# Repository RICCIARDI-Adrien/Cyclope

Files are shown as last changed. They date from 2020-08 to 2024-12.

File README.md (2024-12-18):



# Cyclope

A little robot powered by a Raspberry Pi 3 A+, featuring a 8MPixel Raspberry Pi Camera V2 and a 360° lidar.  
A fast WiFi connection allows to remote control the robot while displaying camera real-time full HD video stream.  
A tailored Buildroot Linux distribution runs the software, controlled through WiFi through an embedded web server.

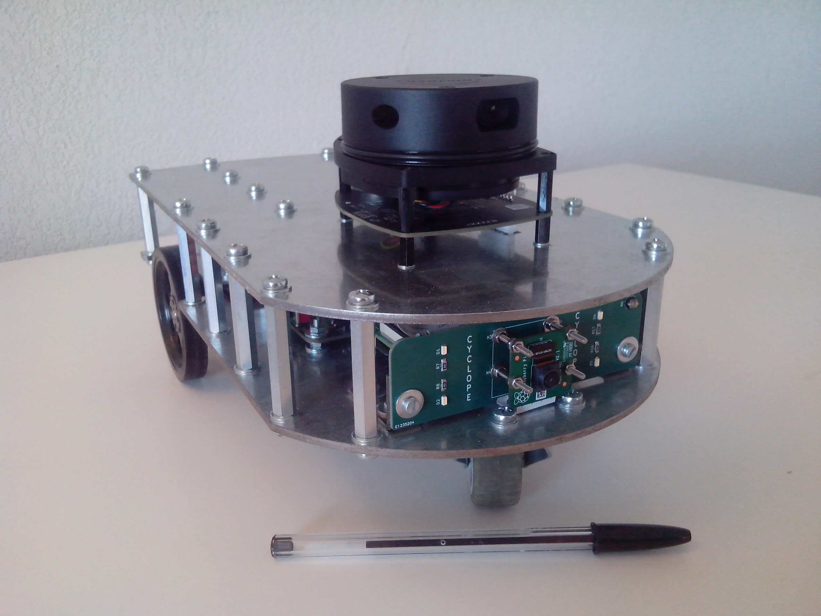
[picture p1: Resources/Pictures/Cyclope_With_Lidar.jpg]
Cyclope


## Hardware

PCB has been designed using KiCad 5.1.5 and has been ported to KiCad 6. All manufacturing files are available from [Release](https://github.com/RICCIARDI-Adrien/Cyclope/releases) page.  
A PDF version of the schematic is also provided.

## Software

Robot's Raspberry Pi is powered by a tailored [Buildroot](https://buildroot.org) Linux distribution.

### Getting sources

Clone the repository and the submodules all in the row :
```
git clone --recurse-submodules https://github.com/RICCIARDI-Adrien/Cyclope
```

### Building

Enter repository directory, clean previous build (if needed) and generate image :
```
cd Cyclope/Software/buildroot
make distclean
make BR2_EXTERNAL=$(realpath ..)/cyclope cyclope_defconfig
make
```

Generated image to burn to a SD card is `Cyclope/Software/buildroot/output/images/sdcard.img`.

## Mechanical

Chassis is made of two overlaid 3mm-thick steel plates.  
See [Mechanical_Dimensions.odg](Chassis/Mechanical_Dimensions.odg) file for additional design information.  
Provide the `Chassis.dxf` file from [Release](https://github.com/RICCIARDI-Adrien/Cyclope/releases) page to a metal laser cutting service.

## Supply parts

See `Bill_Of_Material.csv` file from [Release](https://github.com/RICCIARDI-Adrien/Cyclope/releases) page for PCB parts. All other needed mechanical and electrical parts are listed below.

### Electrical

* 2x servomotor : [Feetech FS5113R](https://www.gotronic.fr/art-servomoteur-fs5113r-25841.htm)
* 40-pin flat cable : [Amphenol FC40150-0](https://fr.farnell.com/amphenol/fc40150-0/cordon-2-54mm-f-f-150mm-40voies/dp/2217617)
* Battery holder : [EM8](https://www.gotronic.fr/art-coupleur-8-piles-lr6-em8-5718.htm), isolate apparent contacts but battery holder ones with adhesive tape to prevent them from touching chassis spacers

### Mechanical

* Front castor wheel : [Guitel 55031100](https://fr.rs-online.com/web/p/roulettes-industrielles/3064300).
* 2x servomotor support : [ASB01](https://www.gotronic.fr/art-support-de-servos-asb01-11637.htm).
* 2x servomotor wheel : [FS5103R-W](https://www.gotronic.fr/art-roue-pour-servomoteur-fs5103r-25857.htm).
* 2x front board flat angle bracket : NFLE2012-20.
* 21x chassis plates M4x40 hex female spacer : [Ettinger 05.04.401](https://fr.farnell.com/ettinger/05-04-401/entretoise-m4x40-vzk/dp/1466794).
* 4x M2x20 screw to attach camera to front board (use three nuts per screw). Using such long screws allow to further protect the camera.
* 12x M2 nut.
* 4x M2.5x25 screws to attach Raspberry Pi to chassis bottom plate (use three nets per screw).
* 12x M2.5 nut.
* 18x M3x10 screw :
  * 8x to attach both servomotors to their support.
  * 4x to attach the two supports to chassis bottom plate.
  * 4x to attach front board flat angle brackets to chassis bottom plate.
  * 2x to attach front board to flat angle brackets.
* 4x M3x15 screw to attach motherboard to chassis bottom plate (use three nuts per screw).
* 30x M3 nut.
* 47x M4x10 screw :
  * 21x to attach female spacers to chassis bottom plate.
  * 4x to attach castor wheel to chassis bottom plate.
  * 1x to prevent battery pack from escaping from robot bottom.
  * 21x to attach chassis top plate to chassis.
* 5x M4 nut.
* Use flat washers of appropriate dimensions if desired.

## Photo gallery

### Castor wheel

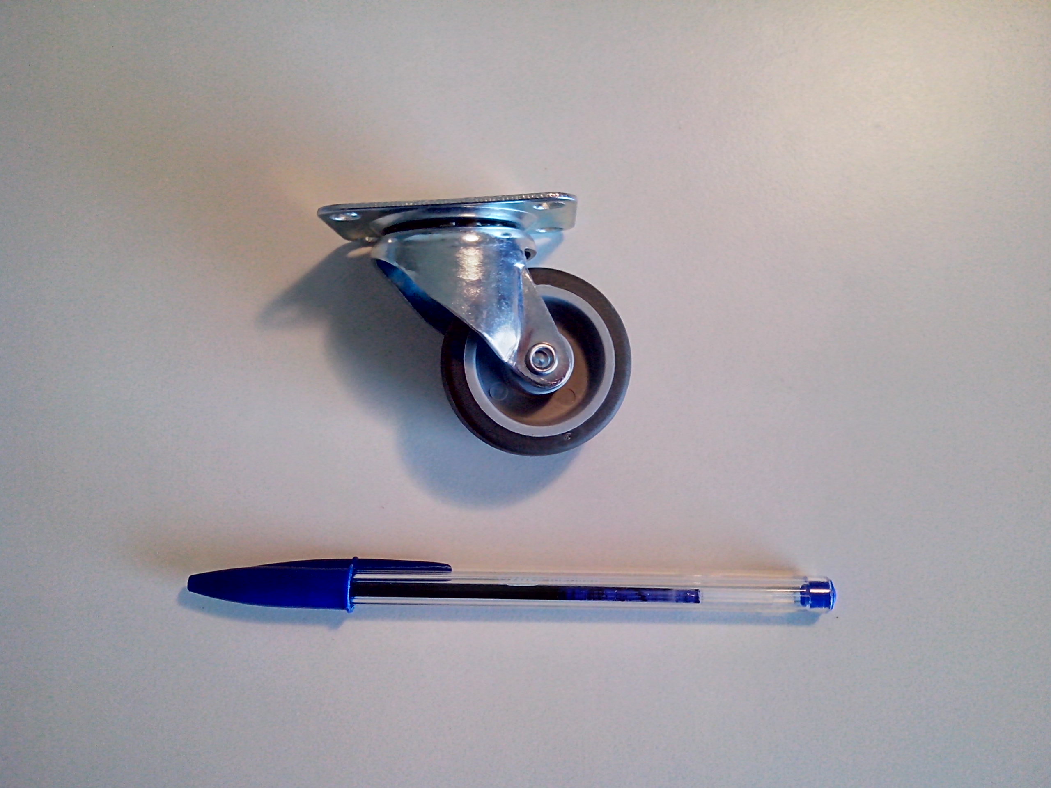
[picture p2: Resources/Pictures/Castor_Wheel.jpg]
Castor wheel


### Servomotor, wheel and support

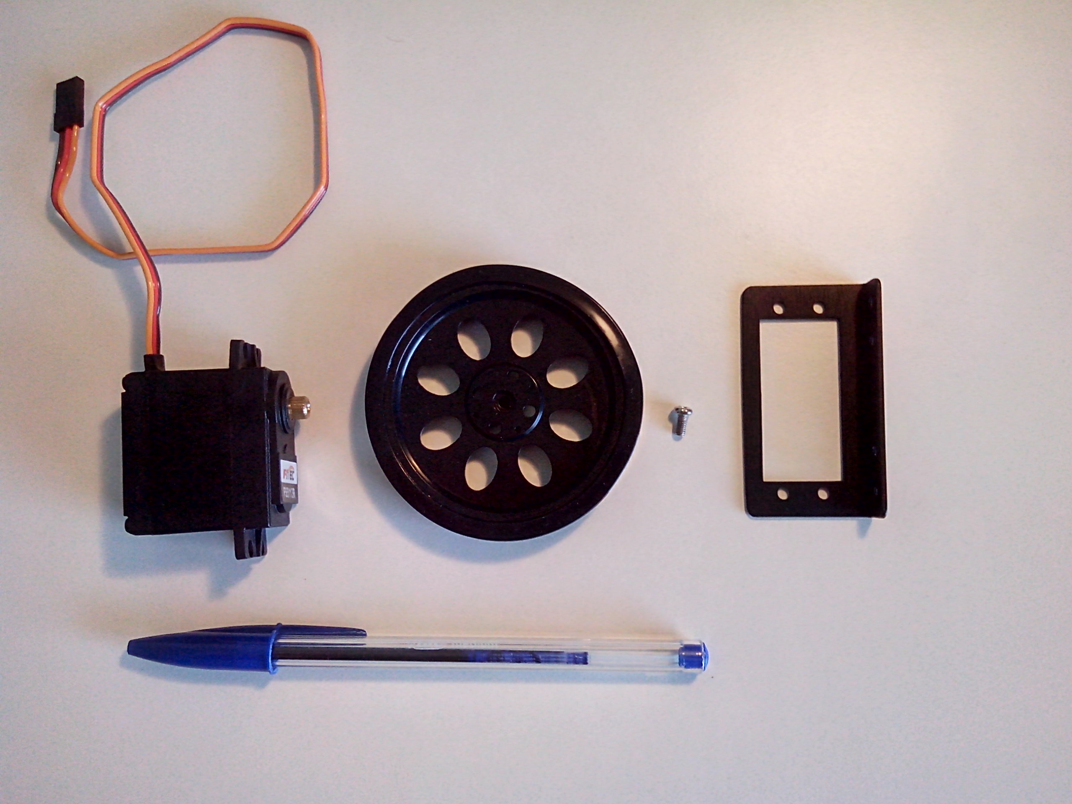
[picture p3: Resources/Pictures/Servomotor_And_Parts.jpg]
Servomotor, wheel and support


### Chassis

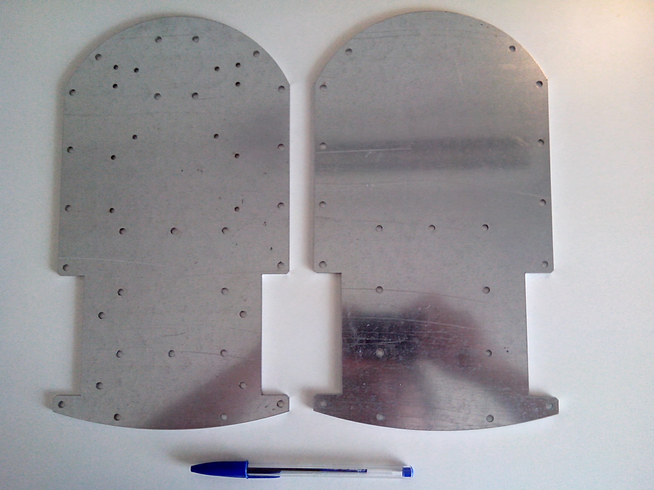
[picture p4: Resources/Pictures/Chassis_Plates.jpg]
Chassis plates

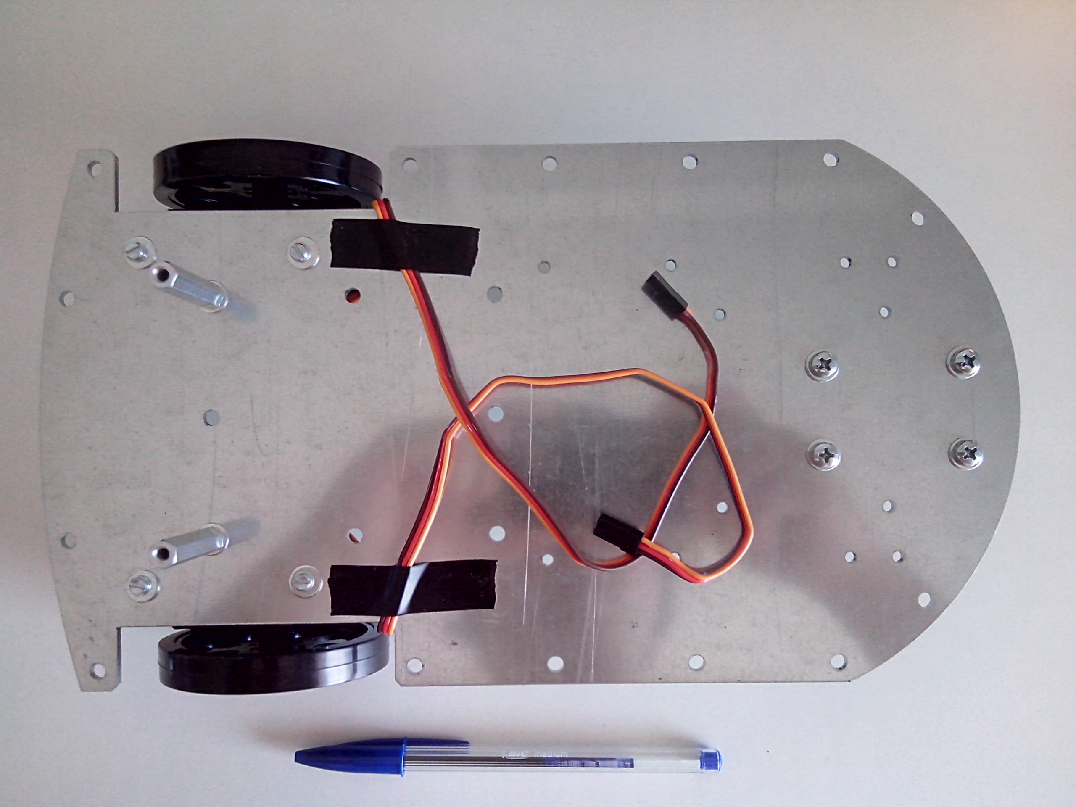
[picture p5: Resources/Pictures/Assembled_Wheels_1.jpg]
Assembled wheels 1

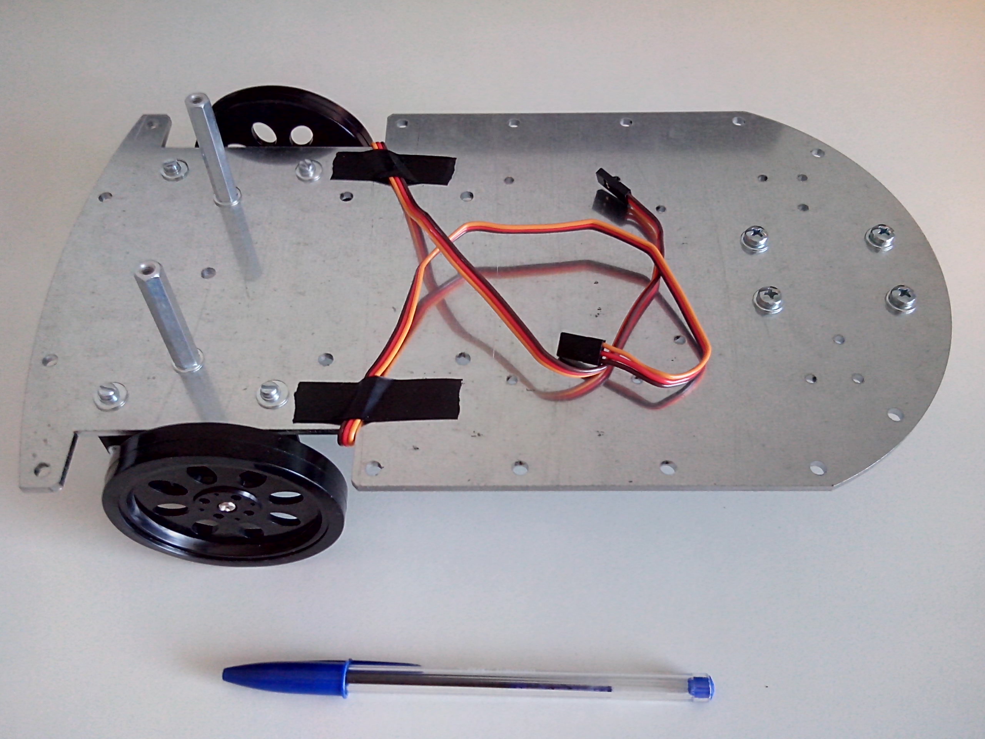
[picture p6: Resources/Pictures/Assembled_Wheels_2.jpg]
Assembled wheels 2

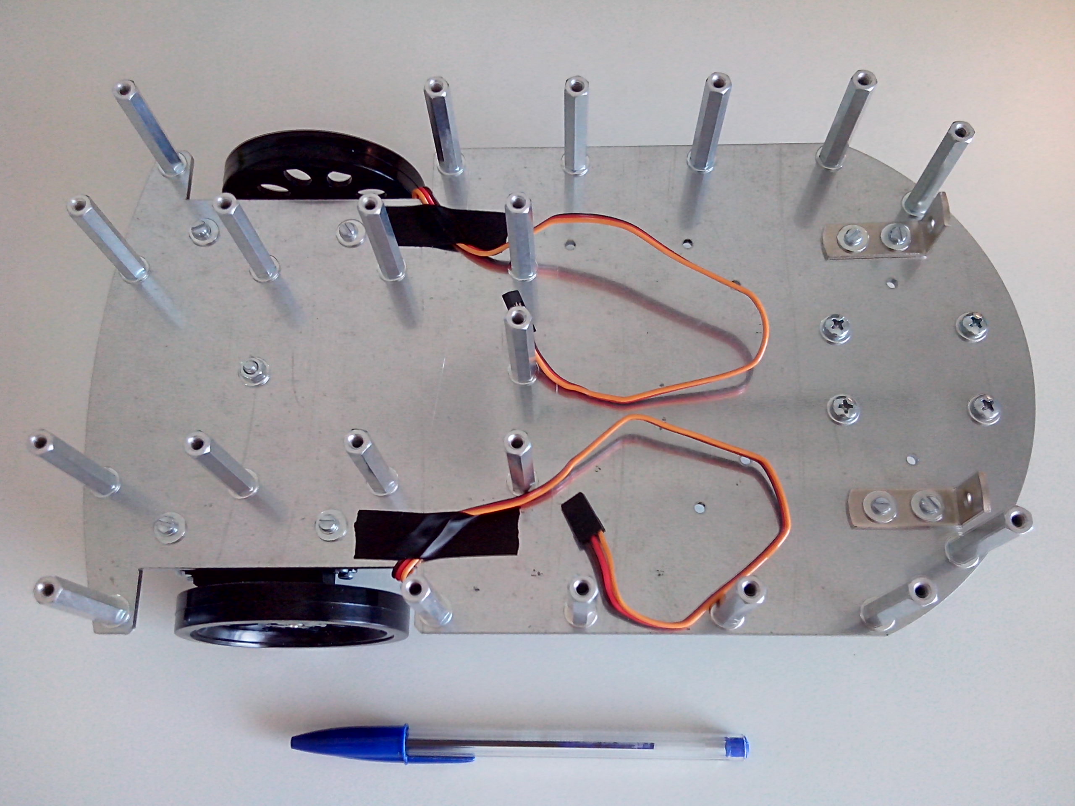
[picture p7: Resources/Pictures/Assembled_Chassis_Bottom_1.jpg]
Assembled chassis bottom 1

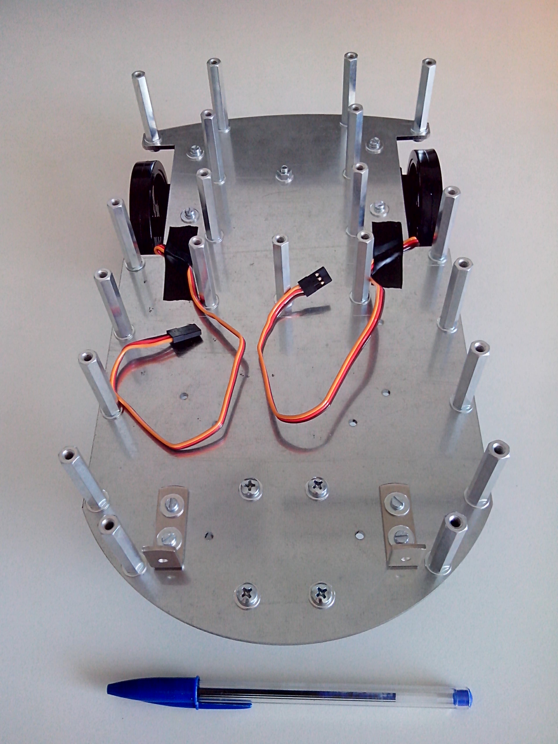
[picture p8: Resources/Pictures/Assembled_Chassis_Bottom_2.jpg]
Assembled chassis bottom 2


### PCB

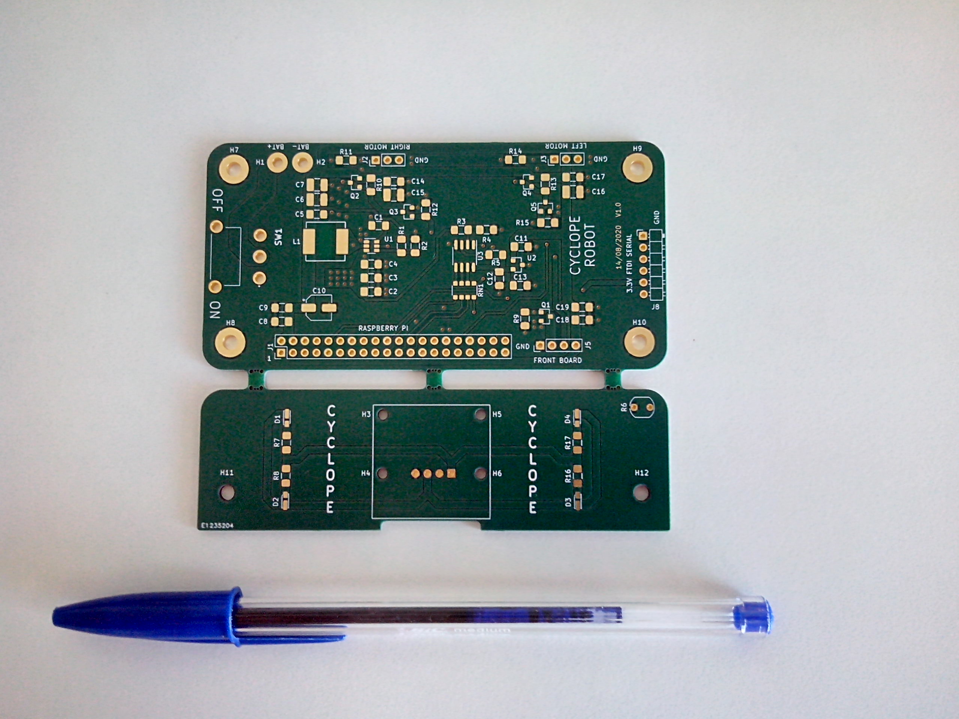
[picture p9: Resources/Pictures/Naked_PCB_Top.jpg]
Naked PCB top

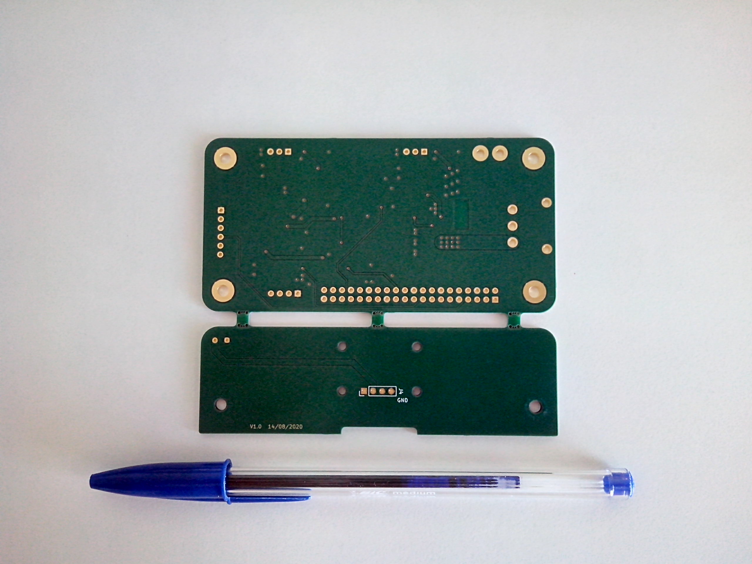
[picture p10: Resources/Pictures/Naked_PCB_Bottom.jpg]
Naked PCB bottom


### Motherboard

PCB has been soldered by hands (resistors array part was missing, I used normal 0805 resistors) :
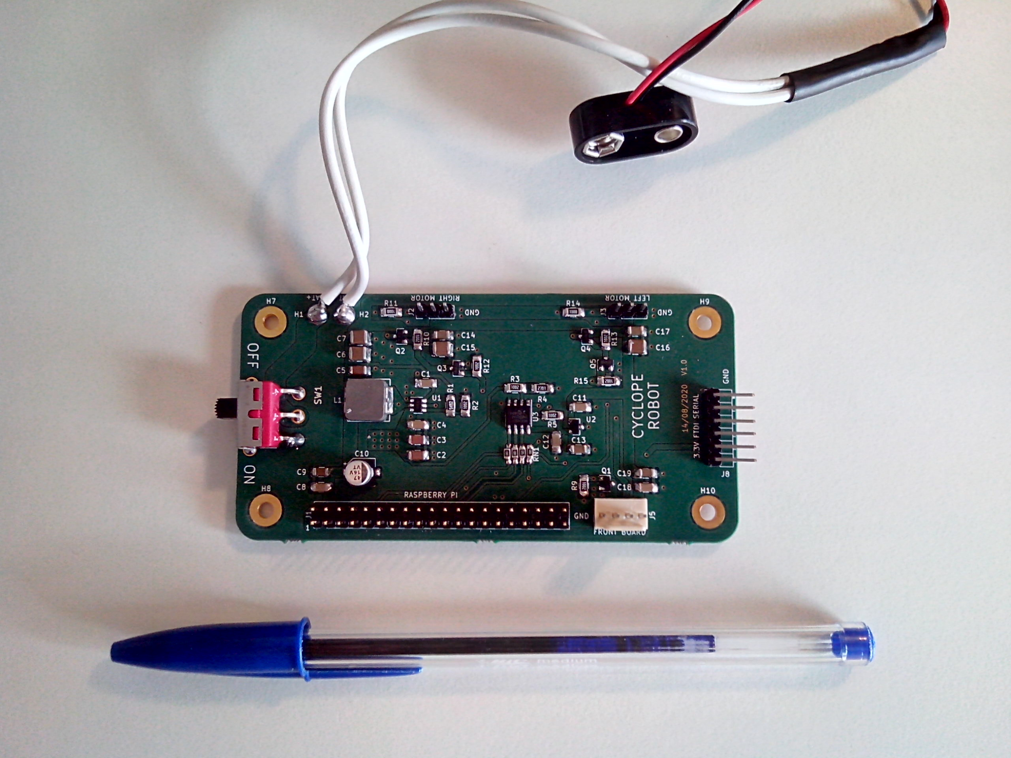
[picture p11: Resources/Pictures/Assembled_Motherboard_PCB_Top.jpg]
Assembled motherboard PCB top

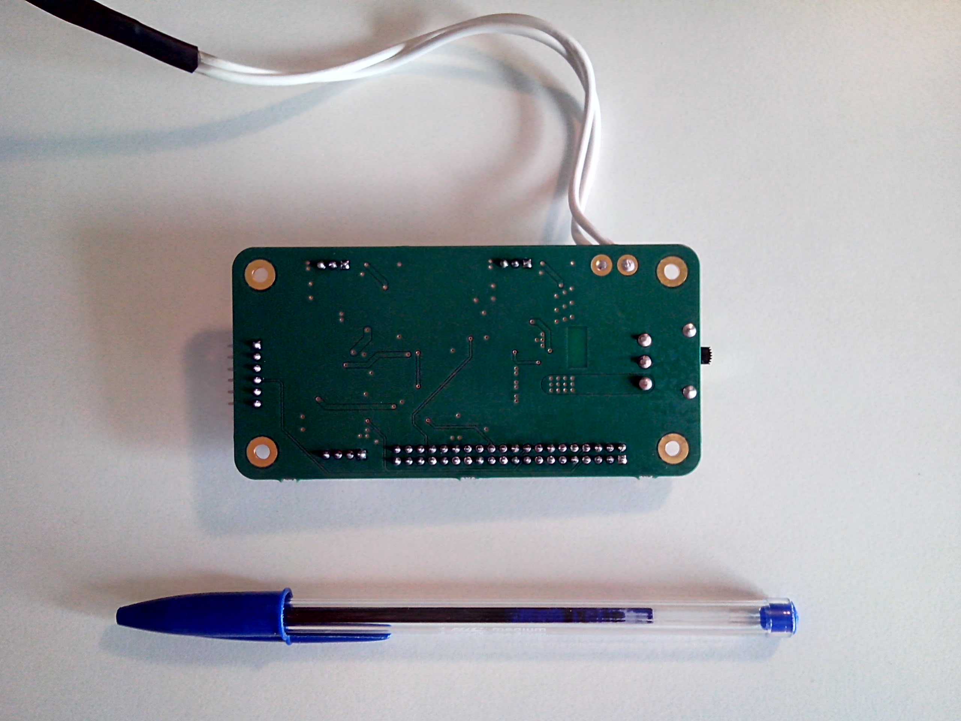
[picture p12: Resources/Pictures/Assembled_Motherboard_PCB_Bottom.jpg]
Assembled motherboard PCB bottom


A big capacitor has been added to keep battery voltage stable when a lot of current is required :
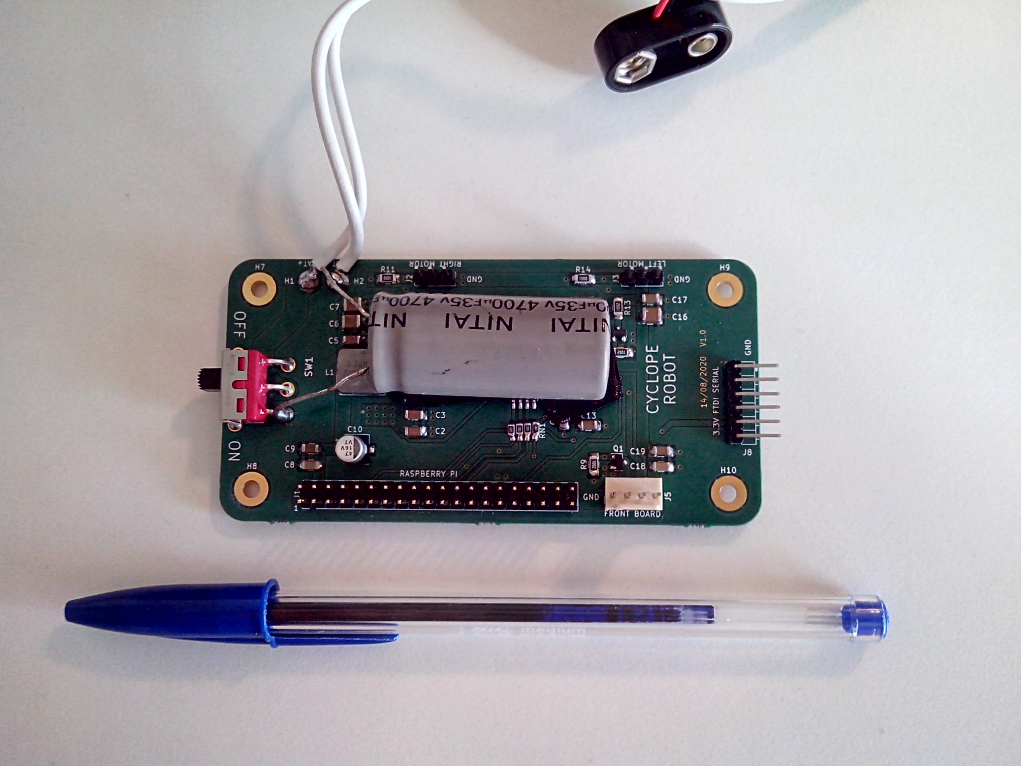
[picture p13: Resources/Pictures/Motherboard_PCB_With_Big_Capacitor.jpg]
Motherboard PCB with big capacitor


### Front board

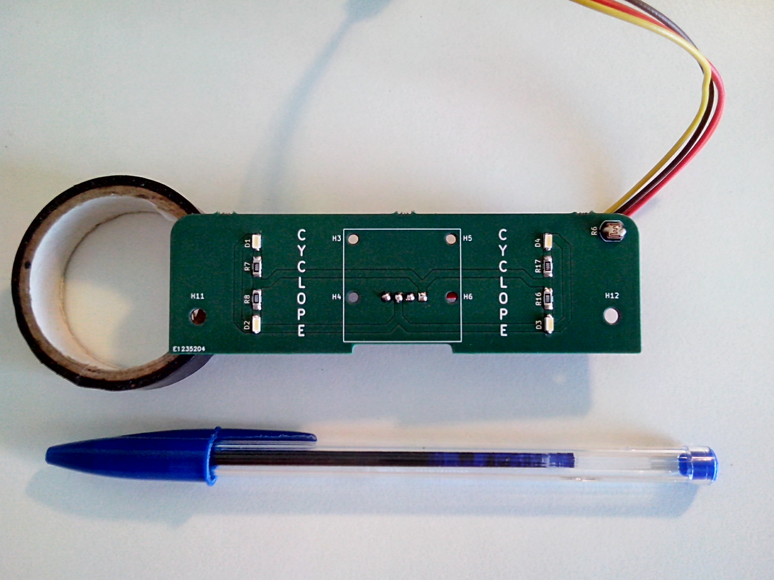
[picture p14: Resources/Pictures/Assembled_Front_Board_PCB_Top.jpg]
Assembled front board PCB top

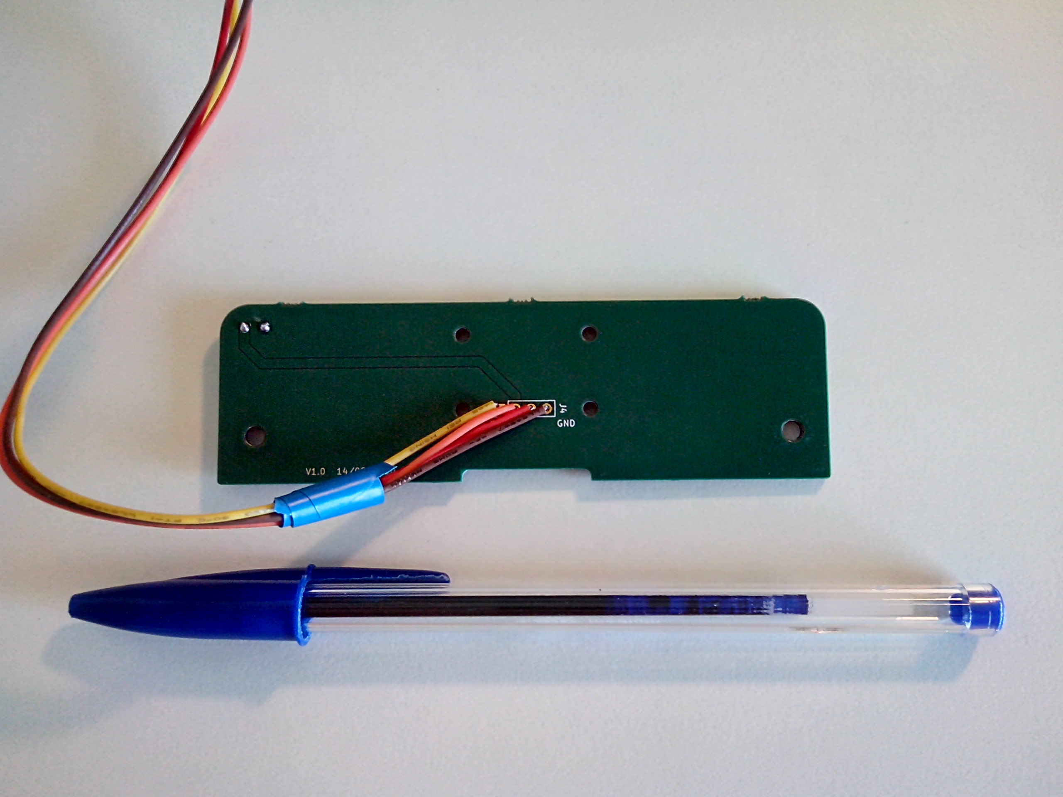
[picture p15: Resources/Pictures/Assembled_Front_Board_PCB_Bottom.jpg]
Assembled front board PCB bottom


With Raspberry Pi Camera V2 mounted :
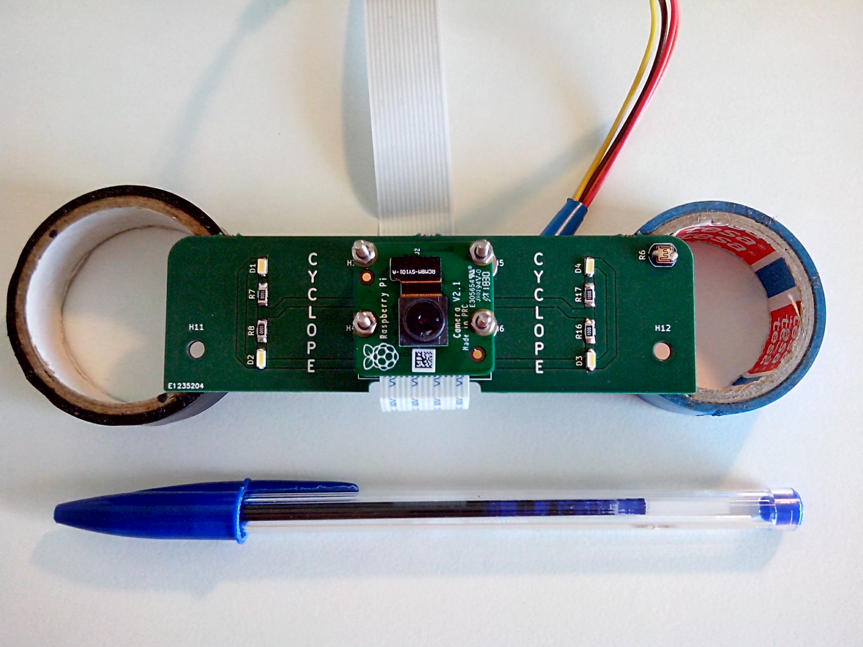
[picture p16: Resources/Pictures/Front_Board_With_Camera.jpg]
Front board with camera


### Assembled electronic boards

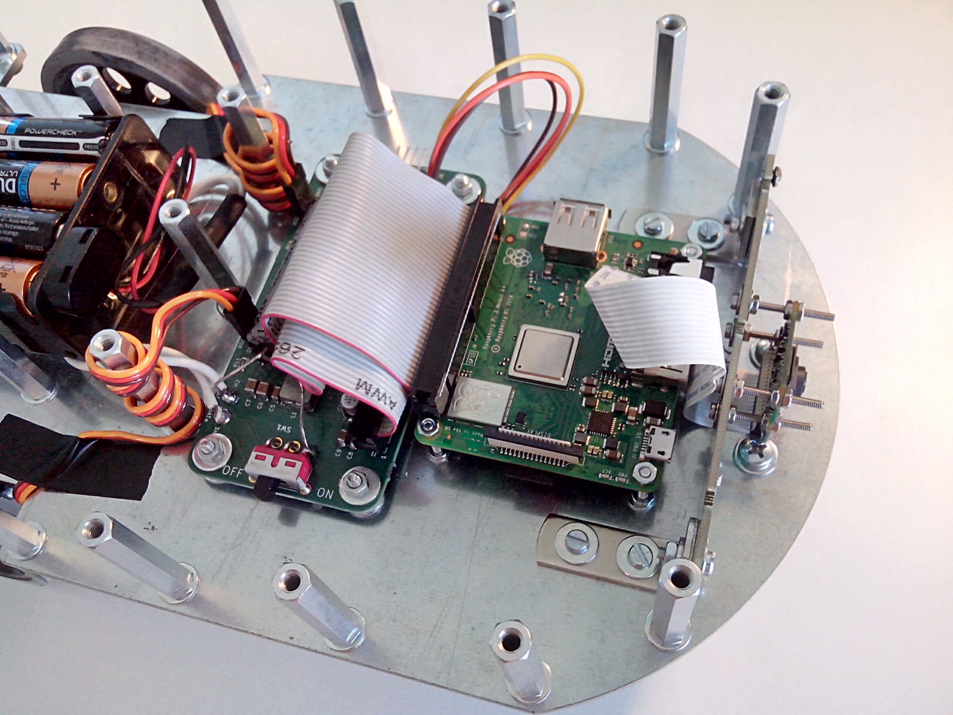
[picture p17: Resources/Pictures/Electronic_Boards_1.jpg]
Electronic boards 1

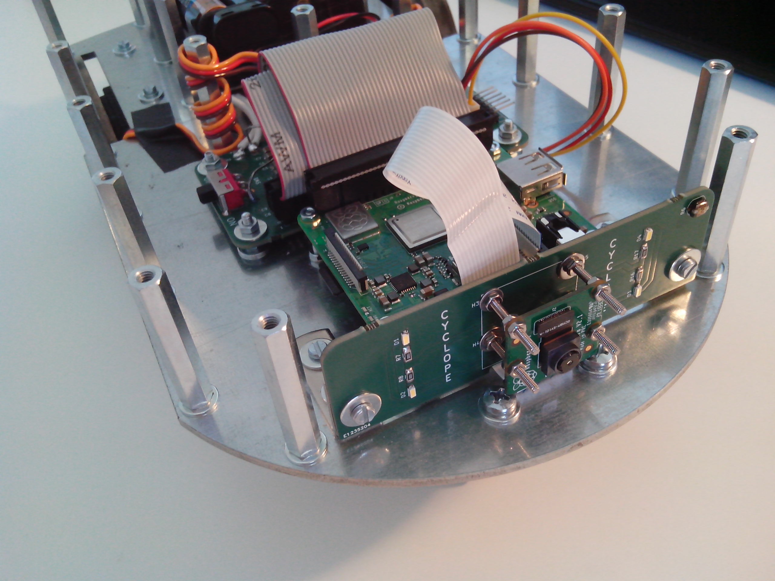
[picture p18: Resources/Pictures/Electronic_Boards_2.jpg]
Electronic boards 2

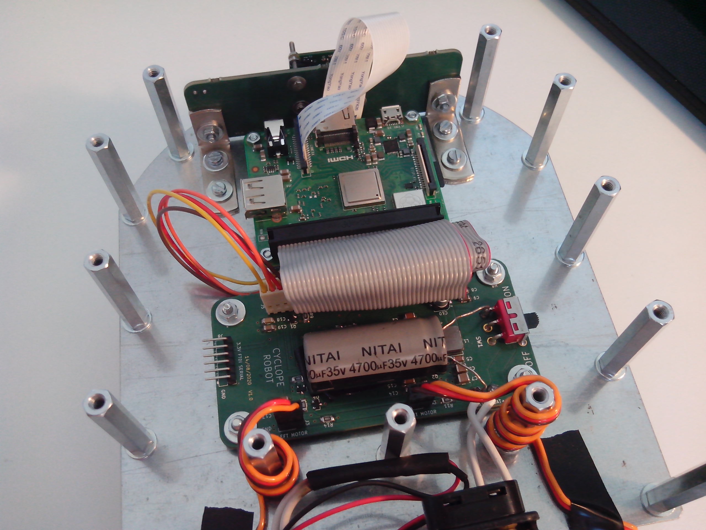
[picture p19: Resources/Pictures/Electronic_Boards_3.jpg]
Electronic boards 3

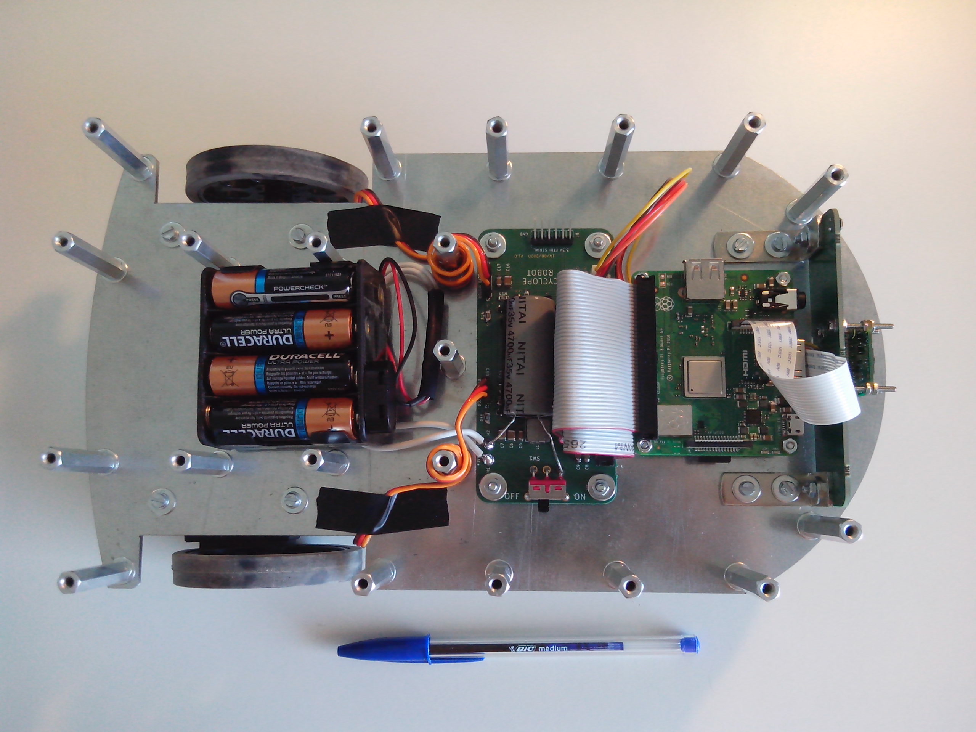
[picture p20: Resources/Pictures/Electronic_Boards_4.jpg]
Electronic boards 4

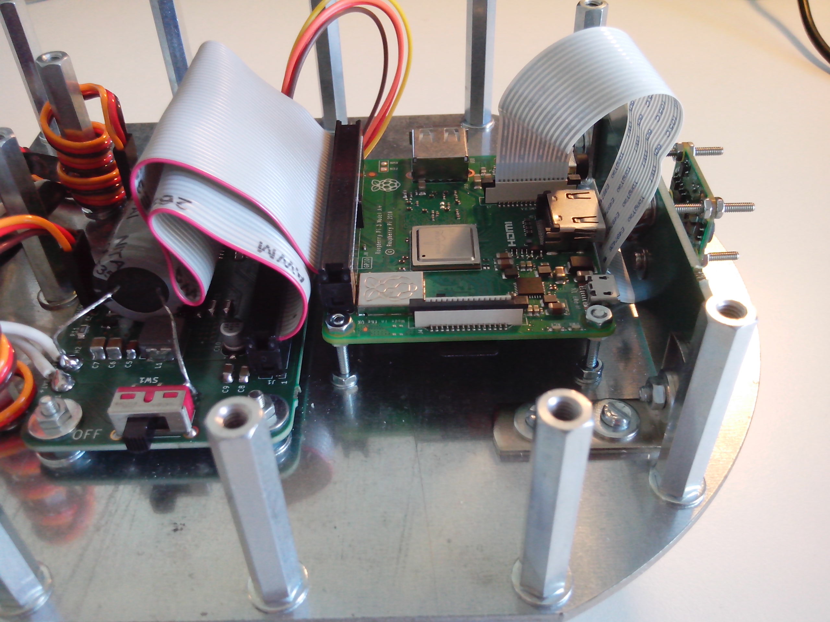
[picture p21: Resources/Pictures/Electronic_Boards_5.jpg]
Electronic boards 5


### Assembled robot

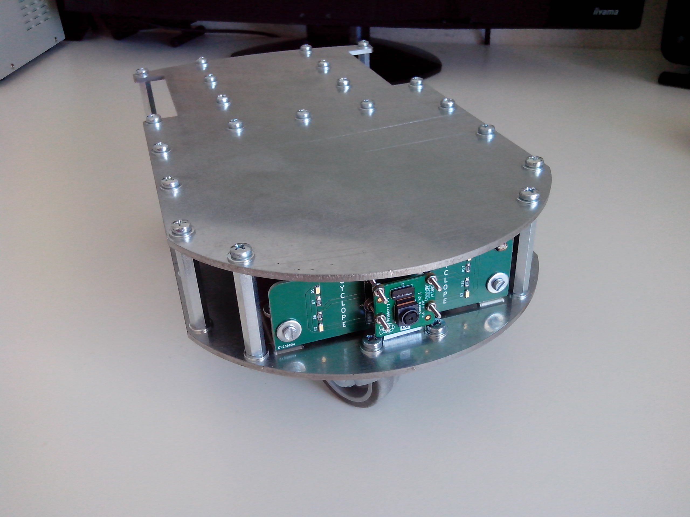
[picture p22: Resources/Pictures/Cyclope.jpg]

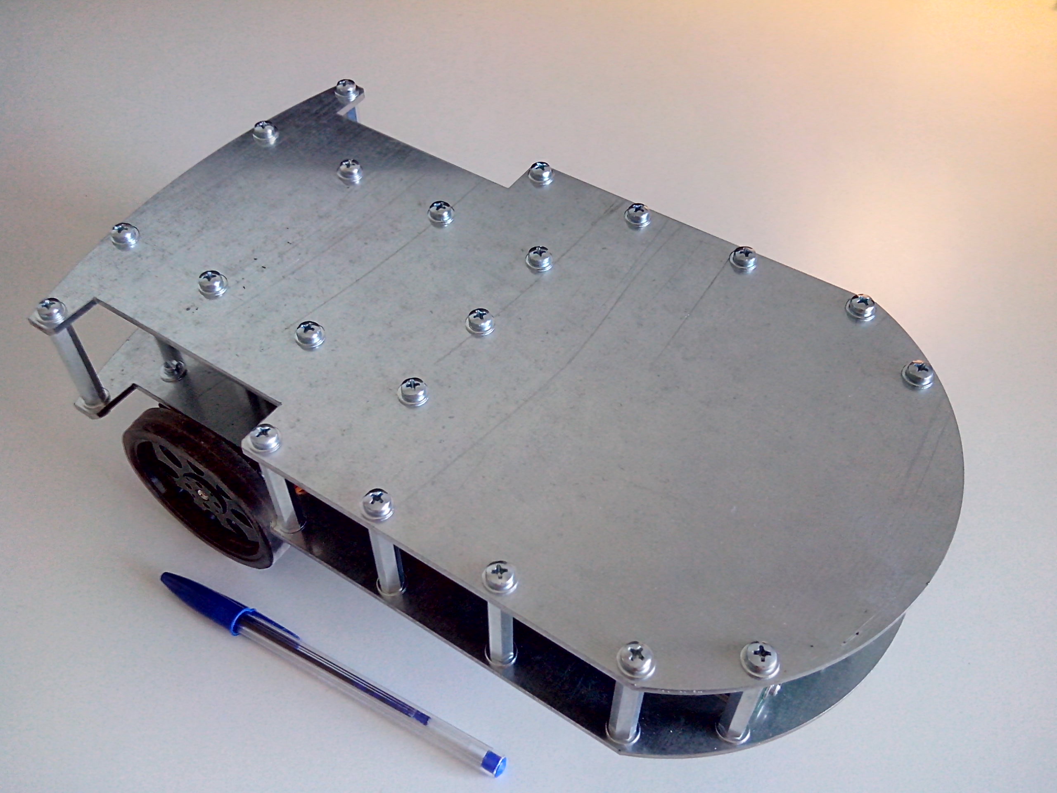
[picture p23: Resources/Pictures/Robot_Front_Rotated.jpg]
Robot front rotated

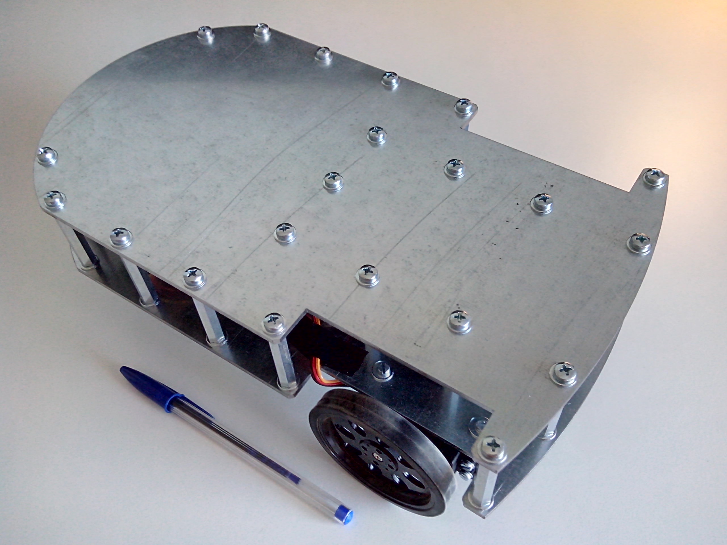
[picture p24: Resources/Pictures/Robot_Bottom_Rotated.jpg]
Robot bottom rotated

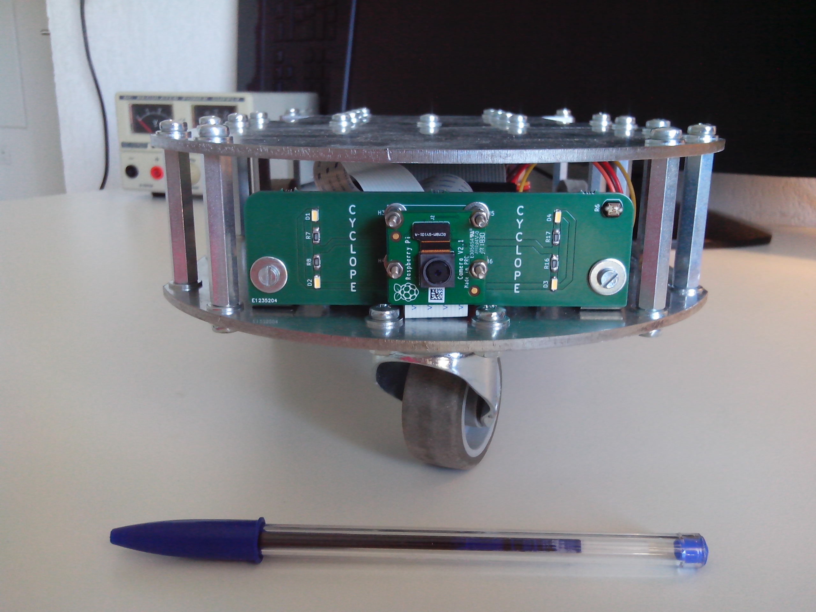
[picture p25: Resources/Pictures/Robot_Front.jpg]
Robot front

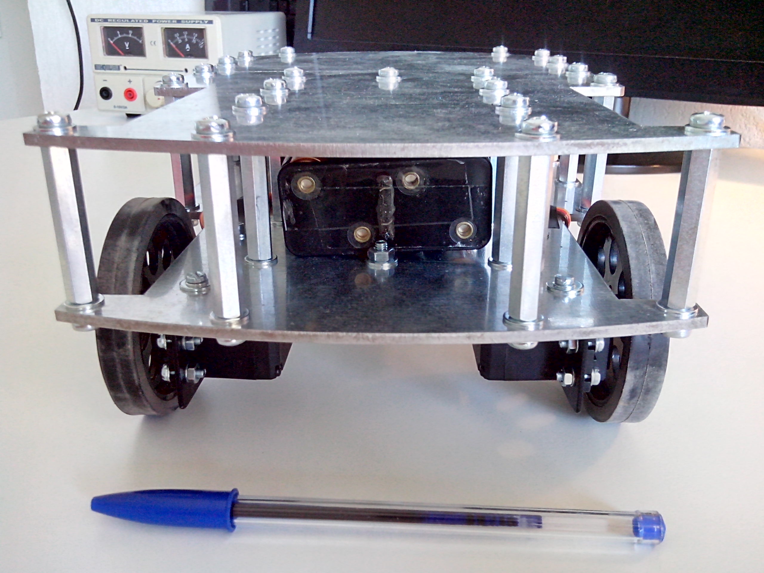
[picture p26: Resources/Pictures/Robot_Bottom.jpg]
Robot bottom

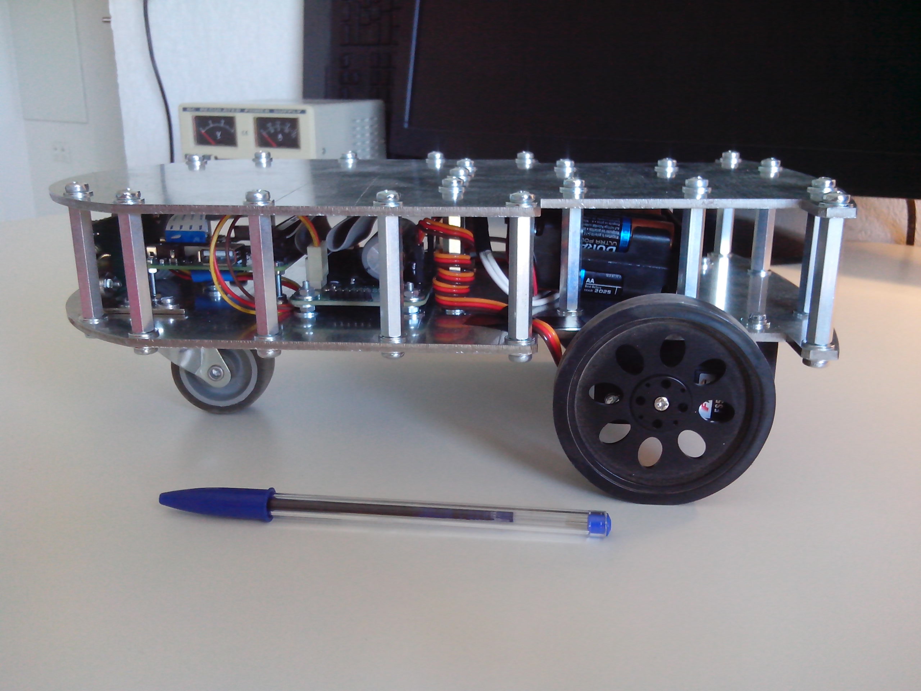
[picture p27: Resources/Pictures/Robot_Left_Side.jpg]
Robot left side

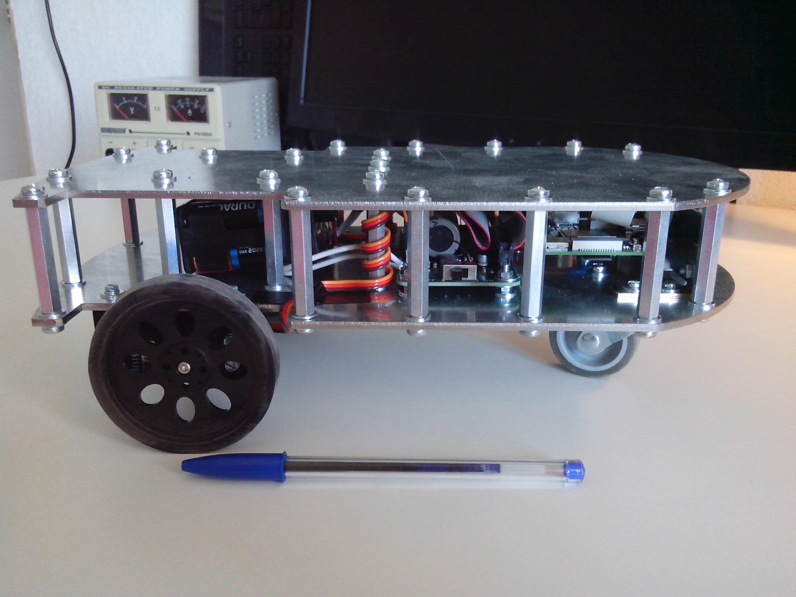
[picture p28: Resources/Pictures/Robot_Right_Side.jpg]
Robot right side


### Update for version 1.1 adding a 360° lidar

Chassis top plate with lidar holes :
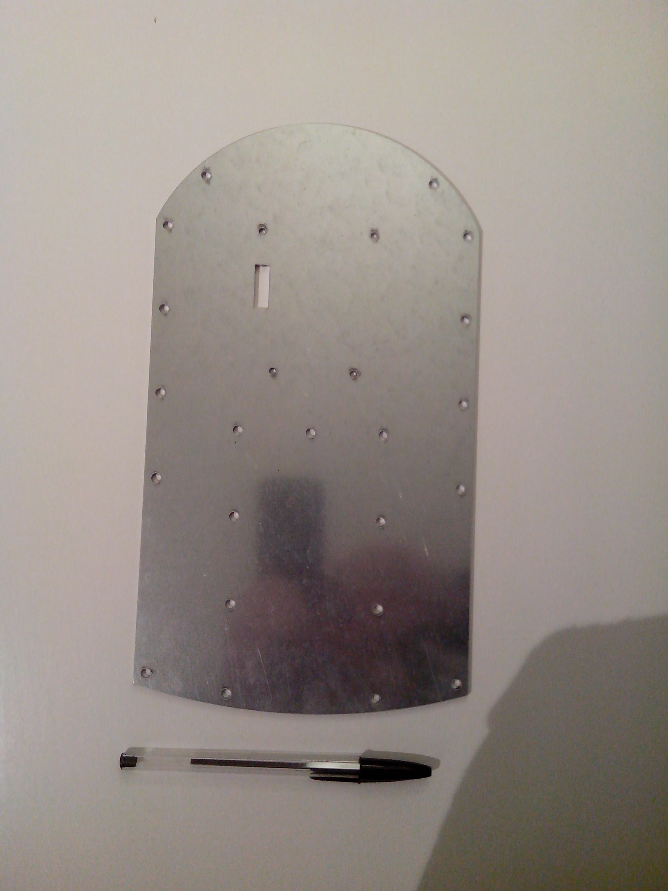
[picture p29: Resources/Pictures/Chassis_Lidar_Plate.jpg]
Chassis top plate


Lidar assembled on chassis top plate :
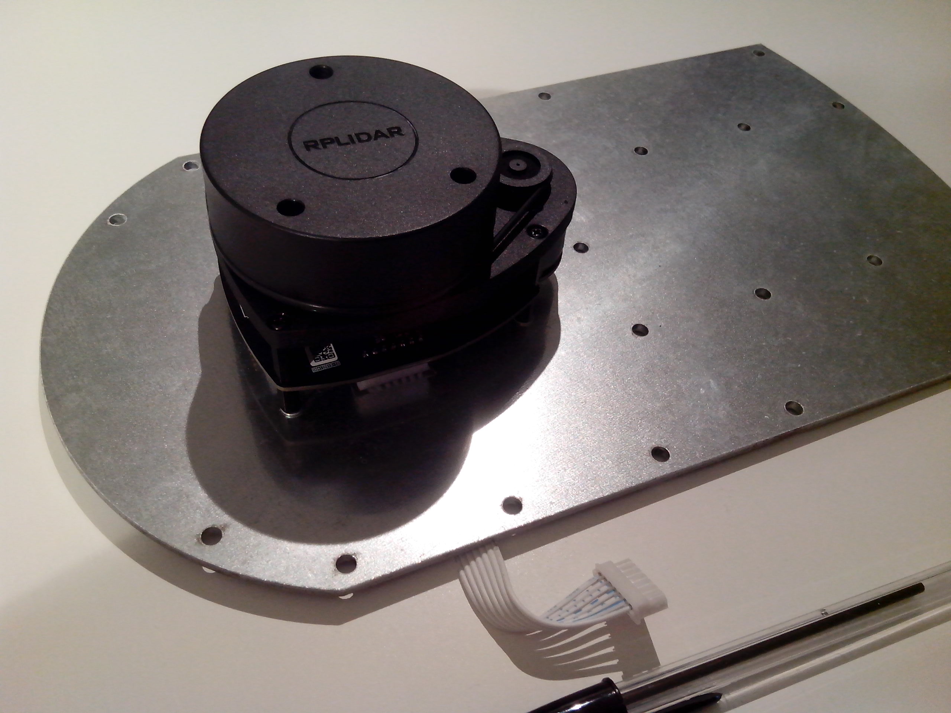
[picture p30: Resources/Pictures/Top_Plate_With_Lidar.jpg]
Lidar on chassis top plate


Motherboard PCB with lidar support :
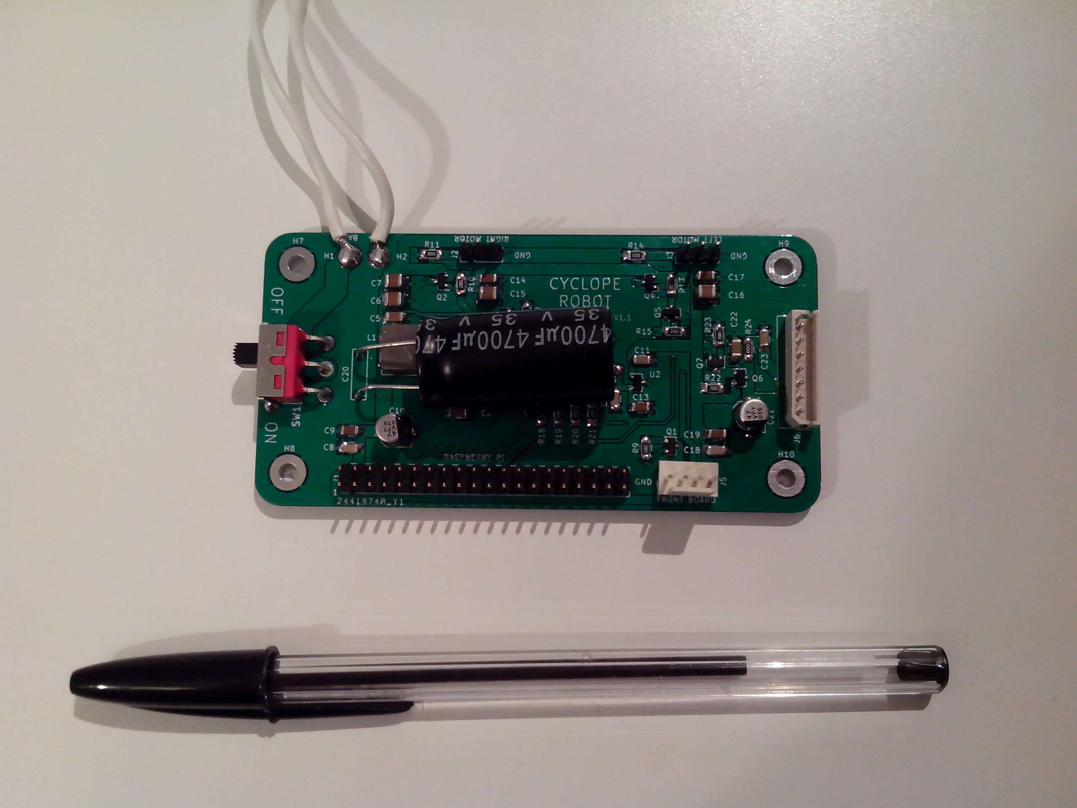
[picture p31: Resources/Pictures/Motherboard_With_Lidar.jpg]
PCB with lidar


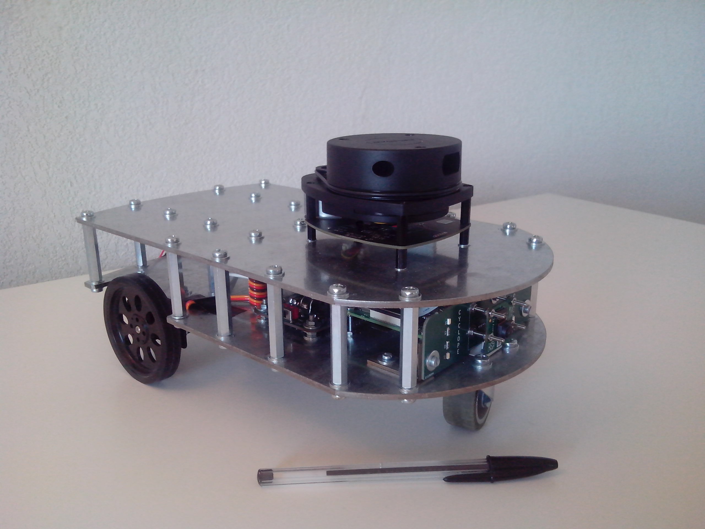
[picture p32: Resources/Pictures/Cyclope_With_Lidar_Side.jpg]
Robot side


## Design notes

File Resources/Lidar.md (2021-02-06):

# Lidar information

## RPLIDAR A1M8 measurements

Measured ripple voltage on core power supply (measured on USB-to-UART board 7-pin connector) :
* Only USB-to-UART board connected to USB (lidar is not connected to USB-to-UART board) : 50 mVpp
* Lidar board connected to USB-to-UART board and running with `frame_grabber` demo : 200 mVpp

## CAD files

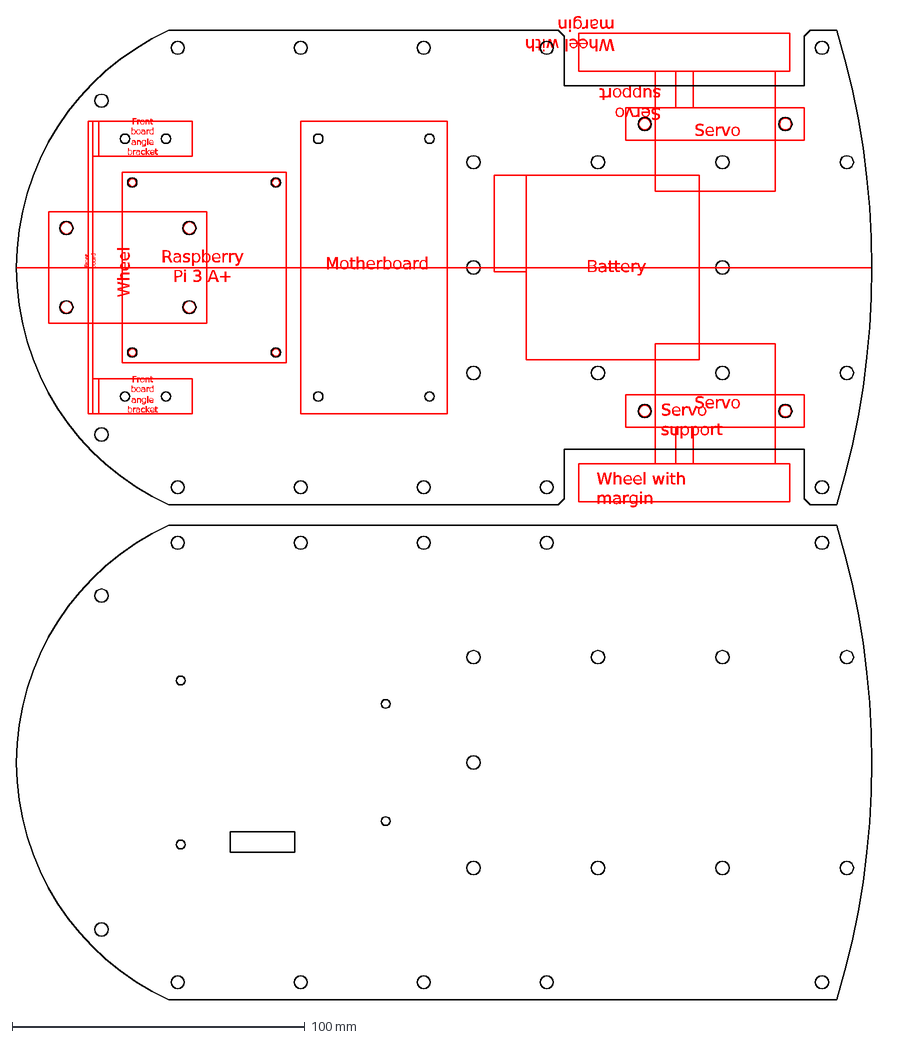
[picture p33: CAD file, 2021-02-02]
Chassis/Chassis.dxf
Motherboard
Front board
angle bracket
Raspberry Pi 3 A+
Wheel
Wheel with margin
Servo support
Servo
Battery

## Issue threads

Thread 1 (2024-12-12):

Bouton utilisateur / Cavalier IO2

RICCIARDI-Adrien, 2024-12-12:
Laisser un cavalier sur IO2 pour le court-circuiter lors de la programmation.

Déplacer le bouton utilisateur sur une GPIO libre (de préférence une GPIO qui a seulement un étage d'entrée).

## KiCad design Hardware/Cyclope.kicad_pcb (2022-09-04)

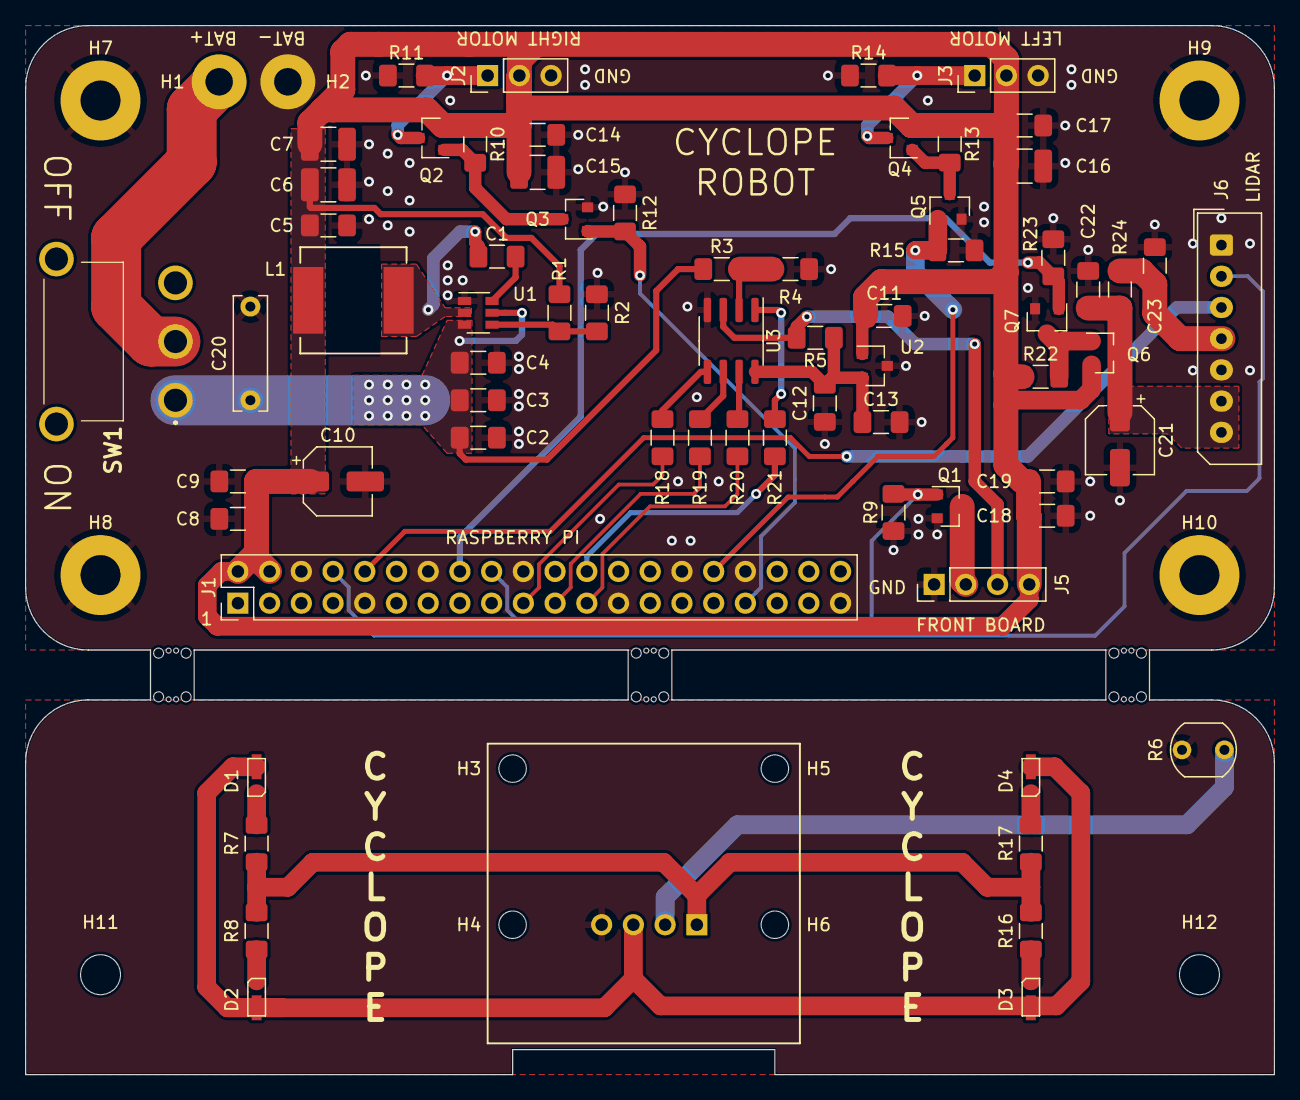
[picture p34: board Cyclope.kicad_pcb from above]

Board: 2 copper layers, 100.0 x 84.0 mm, 88 parts (1 on the bottom side), 40 nets.

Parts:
BAT1: MP000303; Supply_Part
BT1, BT2, BT3, BT4, BT5, BT6: BreakTab; Break_Tab
C1, C4, C8, C11, C12, C18, C23: 100n; C_1206_3216Metric_Pad1.42x1.75mm_HandSolder
C2, C3, C5, C22: 10u; C_1206_3216Metric_Pad1.42x1.75mm_HandSolder
C6, C7, C15, C16: 22u; C_1210_3225Metric_Pad1.42x2.65mm_HandSolder
C9, C13, C14, C17, C19: 2.2u; C_1206_3216Metric_Pad1.42x1.75mm_HandSolder
C10, C21: 47u; CP_Elec_5x5.4
C20: 4700u; C_Rect_L9.0mm_W2.5mm_P7.50mm_MKT
D1, D2, D3, D4: 158301250
H1: BATTERY+; MountingHole_2.2mm_M2_Pad
H2: BATTERY-; MountingHole_2.2mm_M2_Pad
H3, H4, H5, H6: Camera; MountingHole_2.2mm_M2
H7, H8, H9, H10: Motherboard; MountingHole_3.2mm_M3_Pad
H11, H12: Front_Board; MountingHole_3.2mm_M3
J1: M20-9762042; PinHeader_2x20_P2.54mm_Vertical
J2: Motor_2; PinHeader_1x03_P2.54mm_Vertical
J3: Motor_1; PinHeader_1x03_P2.54mm_Vertical
J4, J5: Front; PinHeader_1x04_P2.54mm_Vertical
J6: 22-03-5075; Molex_SPOX_5267-07A_1x07_P2.50mm_Vertical
L1: IHLP3232DZER3R3M01
Q1, Q3, Q5, Q7: DMG3414U; SOT-23
Q2, Q4, Q6: DMG2301L; SOT-23
R1: 54.9K; R_1206_3216Metric_Pad1.42x1.75mm_HandSolder
R2, R3, R5, R9, R10, R12, R13, R15, R22, R23: 10K; R_1206_3216Metric_Pad1.42x1.75mm_HandSolder
R4: 2.7K; R_1206_3216Metric_Pad1.42x1.75mm_HandSolder
R6: LDR07; R_LDR_5.1x4.3mm_P3.4mm_Vertical
R7, R8, R11, R14, R16, R17: 100; R_1206_3216Metric_Pad1.42x1.75mm_HandSolder
R18, R19, R20, R21: 10; R_1206_3216Metric_Pad1.42x1.75mm_HandSolder
R24: 0; R_1206_3216Metric_Pad1.42x1.75mm_HandSolder
SW1: 1101M2S3ABE2; 1101M2S3AQE2
U1: TPS565208DDC; SOT-23-6
U2: NCP51460SN33T1G; SOT-23
U3: MCP3002; SOIC-8_3.9x4.9mm_P1.27mm

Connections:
+3.3VA: C12.1, C13.1, R5.1, U2.2, U3.8
+5V: C5.2, C6.2, C7.2, C8.2, C9.2, C10.1, C11.1, C14.2, C15.2, C16.2, C17.2, C18.2, C19.2, J1.2, J1.4, J2.2, J3.2, J5.4, L1.2, Q2.2, Q4.2, Q6.2, R1.1, R10.1, R13.1, R22.1, U2.1
+5VD: J4.1, R7.1, R8.1, R16.1, R17.1
ADC_SPI_CS: J1.24, R21.2
ADC_SPI_MISO: J1.21, R19.1
ADC_SPI_MOSI: J1.19, R18.1
ADC_SPI_SCK: J1.23, R20.1
BATTERY+: C2.2, C3.2, C4.2, C20.1, R3.1, SW1.1, U1.3, U1.5
FRONT_BOARD_LDR: J5.3, R5.2, U3.3
FRONT_BOARD_LEDS: J1.18, Q1.1, R9.2
GND: C2.1, C3.1, C4.1, C5.1, C6.1, C7.1, C8.1, C9.1, C10.2, C11.2, C12.2, C13.2, C14.1, C15.1, C16.1, C17.1, C18.1, C19.1, C20.2, C21.2, C22.1, C23.2, H2.1, H7.1, H8.1, H9.1, H10.1, J1.6, J1.9, J1.14, J1.20, J1.25, J1.30, J1.34, J1.39, J2.3, J3.3, J5.1, J6.1, J6.5, Q1.2, Q3.2, Q5.2, Q7.2, R2.2, R4.2, R9.1, R11.1, R12.2, R14.1, R15.2, R23.2, U1.1, U2.3, U3.4
GNDD: J4.4, R6.2
LIDAR_ENABLE: J1.16, Q7.1, R23.1
LIDAR_UART_RX: J1.8, J6.2
LIDAR_UART_TX: J1.10, J6.3
unnamed: C1.1, L1.1, U1.2
unnamed: C1.2, U1.6
unnamed: C21.1, C22.2, J6.6, J6.7, Q6.3, R24.2
unnamed: C23.1, J6.4, R24.1
unnamed: D1.1, D2.1, D3.1, D4.1, J4.3
unnamed: D1.2, R7.2
unnamed: D2.2, R8.2
unnamed: D3.2, R16.2
unnamed: D4.2, R17.2
unnamed: H1.1, SW1.2
unnamed: J1.32, Q5.1, R15.1
unnamed: J1.33, Q3.1, R12.1
unnamed: J2.1, Q2.3, R11.2
unnamed: J3.1, Q4.3, R14.2
unnamed: J4.2, R6.1
unnamed: J5.2, Q1.3
unnamed: Q2.1, Q3.3, R10.2
unnamed: Q4.1, Q5.3, R13.2
unnamed: Q6.1, Q7.3, R22.2
unnamed: R1.2, R2.1, U1.4
unnamed: R3.2, R4.1, U3.2
unnamed: R18.2, U3.5
unnamed: R19.2, U3.6
unnamed: R20.2, U3.7
unnamed: R21.1, U3.1

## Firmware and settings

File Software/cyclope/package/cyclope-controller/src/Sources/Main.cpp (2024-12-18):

/** @file Main.cpp
 * Cyclope middleware entry point and AI program execution.
 * @author Adrien RICCIARDI
 */
#include <Adc.hpp>
#include <ArtificialIntelligenceProgramManager.hpp>
#include <cstdlib>
#include <Lidar.hpp>
#include <Light.hpp>
#include <Log.hpp>
#include <Motor.hpp>
#include <unistd.h>
#include <WebServer.hpp>

//-------------------------------------------------------------------------------------------------
// Entry point
//-------------------------------------------------------------------------------------------------
int main()
{
	// Initialize logging before everything else
	Log::initialize();
	LOG(LOG_INFO, "Starting Cyclope controller...");

	// Configure motor PWMs
	if (Motor::initialize() != 0)
	{
		LOG(LOG_ERR, "Motors initialization failed, aborting.");
		return EXIT_FAILURE;
	}

	// Configure front board leds
	if (Light::initialize() != 0)
	{
		LOG(LOG_ERR, "Lights initialization failed, aborting.");
		return EXIT_FAILURE;
	}

	// Configure analog voltages sampling
	if (Adc::initialize() != 0)
	{
		LOG(LOG_ERR, "ADC initialization failed, aborting.");
		return EXIT_FAILURE;
	}

	// Configure Lidar module
	if (Lidar::initialize() != 0)
	{
		LOG(LOG_ERR, "Lidar initialization failed, aborting.");
		return EXIT_FAILURE;
	}

	// Initialize the server
	if (WebServer::initialize() != 0)
	{
		LOG(LOG_ERR, "Web server initialization failed, aborting.");
		return EXIT_FAILURE;
	}

	// Make the robot lights blink three times to tell it is ready
	for (int i = 0; i < 3; i++)
	{
		if (Light::setEnabled(true) != 0) LOG(LOG_ERR, "Failed to turn lights on.");
		usleep(250000);
		if (Light::setEnabled(false) != 0) LOG(LOG_ERR, "Failed to turn lights off.");
		usleep(250000);
	}
	LOG(LOG_INFO, "Server is ready.");

	// Execute AI programs, exploiting the main thread
	while (1)
	{
		// Wait for a program to execute
		LOG(LOG_INFO, "Waiting for an AI program to execute...");
		ArtificialIntelligenceProgramBase *pointerProgram = ArtificialIntelligenceProgramManager::waitForProgramExecutionRequest();
		if (pointerProgram == nullptr)
		{
			LOG(LOG_ERR, "The selected AI program does not exist.");
			continue;
		}

		// Execute the requested program
		LOG(LOG_INFO, "Beginning execution of the AI program \"%s\".", pointerProgram->getDescriptiveName());
		pointerProgram->setExitRequest(false); // Reset the exit flag to make the program run
		pointerProgram->run();

		// Make sure the robot is stopped
		Motor::setRobotMotion(Motor::ROBOT_MOTION_STOP);
		Lidar::setEnabled(false);
		Light::setEnabled(false);
	}

	return EXIT_SUCCESS;
}

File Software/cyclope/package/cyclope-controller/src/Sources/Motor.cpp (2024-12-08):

/** @file Motor.cpp
 * See Motor.hpp for description.
 * @author Adrien RICCIARDI
 */
#include <cstdio>
#include <cstring>
#include <errno.h>
#include <fcntl.h>
#include <Log.hpp>
#include <Motor.hpp>
#include <sys/stat.h>
#include <sys/types.h>
#include <Sysfs.hpp>
#include <unistd.h>

/** The base path of the PWM chip handling the motors PWM channels. */
#define MOTOR_PWM_CHIP_PATH "/sys/class/pwm/pwmchip0"

/** PWM period in nanoseconds (Linux expects nanoseconds). */
#define MOTOR_PWM_PERIOD 20000000 // 20ms
/** Duty cycle in nanoseconds to tell the servomotor to immediately stop. */
#define MOTOR_PWM_STOP_DUTY_CYCLE 1500000

namespace Motor
{
	/** Gather motor-specific parameters. */
	typedef struct
	{
		int pwmChannel;
		int forwardPwmPeriodNanoseconds;
		int backwardPwmPeriodNanoseconds;
	} Motor;

	/** All available motors. */
	typedef enum
	{
		MOTOR_ID_LEFT,
		MOTOR_ID_RIGHT,
		MOTOR_IDS_COUNT
	} MotorId;

	/** All possible motions a motor can perform. */
	typedef enum
	{
		MOTOR_MOTION_STOP,
		MOTOR_MOTION_FORWARD,
		MOTOR_MOTION_BACKWARD
	} MotorMotion;

	/** Direct access to each motor specific settings. */
	static Motor _motors[] =
	{
		// MOTOR_ID_LEFT
		{
			0,
			2000000,
			1000000
		},
		// MOTOR_ID_RIGHT
		{
			1,
			1000000,
			2000000
		}
	};

	/** Check whether a specific PWM channel directory is present, if not tell Linux to make it available.
	 * @param pwmChannel The PWM channel number the motor is connected to.
	 * @return -1 if an error occurred,
	 * @return 0 on success.
	 */
	static int _exportPwmDirectory(int pwmChannel)
	{
		int returnValue = 0;

		// Create the requested PWM directory path
		char stringPwmDirectoryPath[64]; // Buffer is big enough to contain all possible PWM channels
		sprintf(stringPwmDirectoryPath, "/sys/class/pwm/pwmchip0/pwm%d", pwmChannel);

		// Is the sysfs file exported yet ?
		int fileDescriptor = open(stringPwmDirectoryPath, O_RDONLY);
		if (fileDescriptor == -1) // File is not exported, export it
		{
			// Create the string to write to sysfs export file
			char stringPwmChannel[16];
			sprintf(stringPwmChannel, "%d", pwmChannel);

			// Export channel
			if (Sysfs::writeFile(MOTOR_PWM_CHIP_PATH "/export", pwmChannel) != 0)
			{
				LOG(LOG_ERR, "Failed to export PWM channel %d.", pwmChannel);
				returnValue = -1;
			}
			close(fileDescriptor);
		}

		return returnValue;
	}

	/** Tell a motor to move or to stop.
	 * @param motorId The motor to set motion.
	 * @param motorMotion The motion to set.
	 * @return -1 if an error occurred,
	 * @return 0 on success.
	 */
	static int _setMotorMotion(MotorId motorId, MotorMotion motorMotion)
	{
		// Make sure the specified motor exists
		if (motorId >= MOTOR_IDS_COUNT) return -1;

		// Create sysfs file path
		char stringSysfsFile[128];
		sprintf(stringSysfsFile, MOTOR_PWM_CHIP_PATH "/pwm%d/duty_cycle", _motors[motorId].pwmChannel);

		// Set desired duty cycle
		switch (motorMotion)
		{
			case MOTOR_MOTION_STOP:
				if (Sysfs::writeFile(stringSysfsFile, MOTOR_PWM_STOP_DUTY_CYCLE) != 0) return -1;
				break;

			case MOTOR_MOTION_FORWARD:
				if (Sysfs::writeFile(stringSysfsFile, _motors[motorId].forwardPwmPeriodNanoseconds) != 0) return -1;
				break;

			case MOTOR_MOTION_BACKWARD:
				if (Sysfs::writeFile(stringSysfsFile, _motors[motorId].backwardPwmPeriodNanoseconds) != 0) return -1;
				break;

			default:
				LOG(LOG_ERR, "Unknown motor motion requested : %d, ignoring command.", motorMotion);
				return -1;
		}

		return 0;
	}

	int initialize()
	{
		// TODO load motor PWM periods from Configuration module

		// Configure each motor
		char stringPwmDirectoryPath[64], stringTemporary[128];
		for (int i = 0; i < MOTOR_IDS_COUNT; i++)
		{
			// Make PWM settings available for this motor
			if (_exportPwmDirectory(_motors[i].pwmChannel)) return -1;

			// Cache PWM channel path
			sprintf(stringPwmDirectoryPath, MOTOR_PWM_CHIP_PATH "/pwm%d", _motors[i].pwmChannel);

			// Set PWM period (1/50s)
			sprintf(stringTemporary, "%s/period", stringPwmDirectoryPath);
			if (Sysfs::writeFile(stringTemporary, MOTOR_PWM_PERIOD) != 0) return -1;

			// Make sure motor is stopped
			sprintf(stringTemporary, "%s/duty_cycle", stringPwmDirectoryPath);
			if (Sysfs::writeFile(stringTemporary, MOTOR_PWM_STOP_DUTY_CYCLE) != 0) return -1;

			// Enable motor signal
			sprintf(stringTemporary, "%s/enable", stringPwmDirectoryPath);
			if (Sysfs::writeFile(stringTemporary, 1) != 0) return -1;
		}

		return 0;
	}

	int setRobotMotion(RobotMotion robotMotion)
	{
		switch (robotMotion)
		{
			case ROBOT_MOTION_STOP:
				if (_setMotorMotion(MOTOR_ID_LEFT, MOTOR_MOTION_STOP) != 0) return -1;
				if (_setMotorMotion(MOTOR_ID_RIGHT, MOTOR_MOTION_STOP) != 0) return -1;
				break;

			case ROBOT_MOTION_FORWARD:
				if (_setMotorMotion(MOTOR_ID_LEFT, MOTOR_MOTION_FORWARD) != 0) return -1;
				if (_setMotorMotion(MOTOR_ID_RIGHT, MOTOR_MOTION_FORWARD) != 0) return -1;
				break;

			case ROBOT_MOTION_BACKWARD:
				if (_setMotorMotion(MOTOR_ID_LEFT, MOTOR_MOTION_BACKWARD) != 0) return -1;
				if (_setMotorMotion(MOTOR_ID_RIGHT, MOTOR_MOTION_BACKWARD) != 0) return -1;
				break;

			case ROBOT_MOTION_FORWARD_LEFT:
				if (_setMotorMotion(MOTOR_ID_LEFT, MOTOR_MOTION_STOP) != 0) return -1;
				if (_setMotorMotion(MOTOR_ID_RIGHT, MOTOR_MOTION_FORWARD) != 0) return -1;
				break;

			case ROBOT_MOTION_FORWARD_RIGHT:
				if (_setMotorMotion(MOTOR_ID_LEFT, MOTOR_MOTION_FORWARD) != 0) return -1;
				if (_setMotorMotion(MOTOR_ID_RIGHT, MOTOR_MOTION_STOP) != 0) return -1;
				break;

			case ROBOT_MOTION_BACKWARD_LEFT:
				if (_setMotorMotion(MOTOR_ID_LEFT, MOTOR_MOTION_STOP) != 0) return -1;
				if (_setMotorMotion(MOTOR_ID_RIGHT, MOTOR_MOTION_BACKWARD) != 0) return -1;
				break;

			case ROBOT_MOTION_BACKWARD_RIGHT:
				if (_setMotorMotion(MOTOR_ID_LEFT, MOTOR_MOTION_BACKWARD) != 0) return -1;
				if (_setMotorMotion(MOTOR_ID_RIGHT, MOTOR_MOTION_STOP) != 0) return -1;
				break;

			default:
				LOG(LOG_ERR, "Unknown robot motion : %d, ignoring it.", robotMotion);
				return -1;
		}

		return 0;
	}
}

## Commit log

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2020-07-27 [Hardware] Added a switch to turn off power supply.
    [Cyclope.kicad_pcb, Power_Supply.sch]
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2020-07-28 [Hardware] Started ADC schematic sheet. Added ADC, voltage regulator and battery voltage sensing.
    [ADC.sch, Cyclope.kicad_pcb, Cyclope.sch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]
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2020-07-28 [Hardware] Connected ADC to Raspberry Pi through SPI bus.
    [ADC.sch, Raspberry_Pi.sch]
2020-07-28 [Hardware] Added servomotors supply parts and connected them to Raspberry Pi PWMs.
    [ADC.sch, Cyclope.kicad_pcb, Raspberry_Pi.sch]
2020-07-28 [Hardware] Moved servomotors supply parts to main page. Also added servomotors wheels and supports supplies.
    [Cyclope.sch, Raspberry_Pi.sch]
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2020-07-28 [Hardware] Added a transistor to enable leds control from Raspberry Pi.
    [ADC.sch, Camera_Board.sch, Raspberry_Pi.sch]
2020-07-28 [Hardware] Added Raspberry Pi mounting holes to schematic.
    [Cyclope.kicad_pcb, Cyclope.sch]
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2020-07-28 [Software] Changed partitions mapping to double rootfs and provide a dedicated data partition. This will allow to upgrade firmware image while system is running.
    [genimage.cfg]
2020-07-28 [Software] Moved Bluetooth UART to ttyS0 to be able to use ttyAMA0 as system console.
    [config.txt]
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2020-07-29 [Hardware] Added transistors to drive servomotors PWM signal with +5V instead of Raspberry Pi +3.3V.
    [Cyclope.kicad_pcb, Raspberry_Pi.sch]
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2020-07-29 [Hardware] Removed the multiple connectors that were holding the front board, they will be replaced by angle brackets.
    [Camera_Board.sch]
2020-07-29 [Hardware] Renamed 'camera board' to 'front board' as this board is not only carrying the camera.
    [ADC.sch, Cyclope.sch, Front_Board.sch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]
2020-07-29 [Hardware] Added two more leds for a better night lighting.
    [Front_Board.sch]
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2020-07-29 [Hardware] Added leds, connector and round corners to front board PCB.
    [Cyclope.kicad_pcb]
2020-07-29 [Hardware] Added camera holes and a cut for camera cable to front board PCB.
    [Cyclope.kicad_pcb]
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2020-08-12 [Software] Moved Raspberry Pi embedded software to a dedicated directory to make room for PC application.
    [config.txt, genimage.cfg]
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2020-08-16 [Chassis] Added second motor block and positionned both motor blocks.
    [Chassis.dxf]
2020-08-16 [Chassis] Moved construction drawings to a dedicated layer, so it is easy to remove the constrution layer before exporting to manufacturer.
    [Chassis.dxf]
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2020-08-16 [Chassis] Added battery pack position and fixing holes.
    [Chassis.dxf]
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2020-08-16 [Chassis] Added Raspberry Pi 3 A+ (but not positionned for now), increased battery holding area to ease battery pack insertion and removal.
    [Chassis.dxf]
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2020-08-16 [Chassis] Added front board angle brackets (not positionned for now).
    [Chassis.dxf]
2020-08-16 [Chassis] Positionned front board angle brackets in relation to Raspberry Pi.
    [Chassis.dxf]
2020-08-16 [Hardware] Increased front board PCB size to match chassis dimensions.
    [Cyclope.kicad_pcb]
2020-08-16 [Hardware] Changed front board mounting holes footprint to match angle bracket holes and positionned holes on front board PCB.
    [Cyclope.kicad_pcb, Front_Board.sch]
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2020-08-16 [Hardware] Gathered all motherboard components to a fake PCB to try PCB panelling options.
    [Cyclope.kicad_pcb]
2020-08-16 [Hardware] Added test breaking tabs to PCB to be able to determine PCB production needs.
    [Cyclope.kicad_pcb, Front_Board.sch]
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2020-08-16 [Hardware] Set final motherboard PCB width, added rounded corners to motherboard PCB.
    [Cyclope.kicad_pcb]
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2020-08-16 [Hardware] Fixed ADC voltage reference decoupling capacitors footprints.
    [ADC.sch]
2020-08-16 [Hardware] Fixed bad footprints and duplicated break tab footprints.
    [ADC.sch, Cyclope.kicad_pcb, Front_Board.sch]
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2020-08-16 [Hardware] Changed motherboard connector to front board footprint and added more marking to motherboard PCB.
    [Cyclope.kicad_pcb, Front_Board.sch]
2020-08-16 [Hardware] Set default pad to mask clearance and solder mask minimum width values in PCB rules.
    [Cyclope.kicad_pcb]
2020-08-16 [Hardware] Fixed a Edge.Cuts layer line width in PCB.
    [Cyclope.kicad_pcb]
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2020-08-16 [Chassis] Moved motor blocks to the bottom of the chassis to put robot mass at the center, added more fixing supports to battery block.
    [Chassis.dxf]
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2020-08-16 [Chassis] Added bottom plate fixation holes.
    [Chassis.dxf]
2020-08-16 [Chassis] Added bottom plate fixations for components, added top plate.
    [Chassis.dxf]
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2020-08-16 [Hardware] Added larger tracks and a return path for motherboard PCB +5V.
    [Cyclope.kicad_pcb]
2020-08-16 [Hardware] Changed some motherboard connectors connection type with ground planes to decrease impedance.
    [Cyclope.kicad_pcb]
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2020-08-16 [Hardware] Used slightly narrower tracks for ADC SPI bus to have more clearance between 40-pin connector pins.
    [Cyclope.kicad_pcb]
2020-08-16 [Hardware] Improved motherboard PCB to use a 0.25mm trace clearance.
    [Cyclope.kicad_pcb]
2020-08-16 [Chassis] Fixed chassis contour not being well closed.
    [Chassis.dxf]
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2020-08-16 [Chassis] Removed two minuscule cicles that were confusing metal laser cutting service.
    [Chassis.dxf]
2020-08-16 [Chassis] Removed battery blocking screw hole from top plate as it is used only by bottom plate.
    [Chassis.dxf]
2020-08-16 [Hardware] Removed mechanical supply parts unrelated with PCB, added battery holder supply part.
    [Cyclope.kicad_pcb, Cyclope.sch, Power_Supply.sch]
2020-08-16 [Hardware] Changed 22u capacitors footprint from 1206 to 1210 as more references are available in 1210 package.
    [Cyclope.kicad_pcb, Power_Supply.sch, Raspberry_Pi.sch]
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2020-08-26 [Hardware] Replaced in schematic hard to find resistors array using 2012 package by classic 1206 discrete resistors.
    [ADC.sch]
2020-08-26 [Hardware] Replaced resistors array by discrete resistors in PCB.
    [Cyclope.kicad_pcb]
2020-08-26 [Hardware] Inverted Raspberry Pi UART RX and TX in schematic.
    [Raspberry_Pi.sch]
2020-08-26 [Hardware] Inverted Raspberry Pi UART RX and TX in PCB.
    [Cyclope.kicad_pcb]
2020-08-26 [Hardware] Added a big capacitor right after power supply switch to keep battery voltage stable during high current demands.
    [Power_Supply.sch]
2020-08-26 [Hardware] Added big capacitor 'custom' footprint to PCB. Capacitor must be bent over SMD parts and glued like shown in pictures.
    [Cyclope.kicad_pcb, Power_Supply.sch]
2020-08-26 [Software][Cyclope controller] Removed some information log messages written on startup to avoid bloating system logs.
    [Main.cpp]
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2020-08-30 [Software][Cyclope controller] Improved battery voltage value stability by using a moving average.
    [Adc.cpp]
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2020-10-18 [Software][Cyclope controller] Improved tennis ball detection by discarding the smallest noise objects (ball is assumed to be the biggest object in the frame).
    [ArtificialIntelligenceProgram.cpp]
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2021-02-01 [Chassis] Removed top part hole above wheels to give more protection to wheels.
    [Chassis.dxf]
2021-02-02 [Chassis] Added RPLIDAR A1M8 fixation holes to chassis top.
    [Chassis.dxf]
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2021-02-06 [Hardware] Added missing PCB assembly name to IHLP3232DZER3R3M01 inductor footprint.
    [Cyclope.kicad_pcb]
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2021-03-09 [Software][Cyclope controller] Fixed a bug in lidar UART configuration.
    [Lidar.cpp]
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2021-03-20 [Software][Cyclope controller] Started lidar measures angle computation (some angles are wrong for now).
    [Lidar.cpp]
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2021-03-21 [Hardware] Mirrored lidar connector as connector datasheet numbering does not match lidar datasheet numbering.
    [Cyclope.kicad_pcb, Lidar.sch]
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2021-03-28 [Software][Cyclope controller] Added the begining of the 'wander with no goal' AI program. It is currently able to avoid not too close obstacles.
    [ArtificialIntelligenceProgramWanderWithNoGoal.cpp]
2021-03-28 [Software][Cyclope controller] Added a safety behavior to the 'wander with no goal' AI program to deal when an obstacle is too close to the robot.
    [ArtificialIntelligenceProgramWanderWithNoGoal.cpp]
2021-04-05 [Software][Cyclope controller] Replaced 'wander with no goal' program logic by a state machine to be able to create a more complex backward direction moving sequence.
    [ArtificialIntelligenceProgramWanderWithNoGoal.cpp]
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2021-04-06 [Software][Cyclope controller] Fixed turn in the selected direction during 'wander with no goal' Ai program backward sequence.
    [ArtificialIntelligenceProgramWanderWithNoGoal.cpp]
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2024-12-01 [Software] Updated the Buildroot configuration to generate a 64-bit image instead of the 32-bit one.
    [config.txt, genimage.cfg]
2024-12-01 [Software] Doubled the Buildroot FAT partition to accomodate for the increasing amount of device tree overlays.
    Also set a fixed size for the A/B partitions, this is cleaner than hardcoding offsets.
    [genimage.cfg]
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2024-12-15 [Software][Cyclope controller] Avoid memory leak in the web server if a page content generation failed.
    [WebServer.cpp]
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2024-12-18 [Software][Cyclope controller] Replaced the main menu web page links by buttons.
    [WebServer.cpp]
2024-12-18 [Software][Cyclope controller] Replaced all the web page 'back' links by buttons.
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2024-12-18 [Software] Moved Buildroot and the external tree directly to the Software directory.
    [config.txt, genimage.cfg]
2024-12-20 [Software][Cyclope controller] Added a watchdog timer that needs to be cleared repeatedly by the opened web page to avoid stopping the robot.
    This watchdog triggers when the web server connection is lost and immediately stops the robot.
    [WebServer.cpp]
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
